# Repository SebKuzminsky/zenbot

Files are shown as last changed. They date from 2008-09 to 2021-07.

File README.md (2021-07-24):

This configuration is for the Zenbot CNC Mini Router (2007 version)
with 7i30 driver board, using the Mesa 5i23 for pwm generation &
quadrature counting.

Each axis/joint is run by a servo controlled by a 7i30.  All the servos
have no index channel, instead the index channel is used for home/limit
switches, plus the tool length offset switch.

# Spindle

The spindle is a TB-350S from Wolfgang Engineering (Richard?).

Rated for 0.0001 runout expected, 0.0004 runout max.

20,000 or 25,000 RPM, it's unclear.

Chris Radek has one, and has worked out how to replace the spindle
bearings.

The spindle uses an O-ring as a drive belt.  I got these from the local
hardware store, both seem to work:

* 2 1/16" OD, 1 7/8" ID, 3/32" wall
* 2 1/8" OD 1 7/8" ID, 1/8" wall

# Work holding

There is not much cutting force on the work, the main job of work holding
is to keep the copper surface parallel to XY across the whole work piece.

I used Target or Scotch branch "permanent double sided tape", it seemed
to work.

FIXME: note new tape, easier to work with since it has paper backing on
one side

Chris Radek says:

    I use the thicker tape with filaments in it that's meant for making
    very poor quality installations of tile or maybe carpet?

    Duck brand "Indoor Heavy Duty Carpet Tape"

    <https://www.findtape.com/shop/product-images.aspx?pid=646>

Try NYC CNC's technique of "blue painter's tape/ca/blue painter's tape":
<https://www.youtube.com/watch?time_continue=628&v=r6DCvtcU8_M>

# Z touch off

Bring the tool down close to the work, then raise it 0.001 at a time
until you can just barely roll a precision ground dowel pin between the
tool and the work.  The pins at SSD have a diameter of 0.250 +- 0.001.

If you don't have a dowel pin, the shank of a cutter works too but make
sure you measure the actual diameter carefully.

# Copper clad board

The work table can hold up to 4" x 6" boards.

I've been using MG Chemicals #506:

    Proto Board Copper Clad FR4
    Single Sided
    1 oz.
    6.00" x 4.00" (152.4mm x 101.6mm)
    the copper layer is 0.0014 inch (0.036 mm) thick
    the board is 1.6 mm (.0630 inch) thick

$7.14 from Digi-Key.

# Cutting Tools with Speeds and Feeds

## PreciseBits RCC08-0315-026F

Fish-tail chip breaker router bit, 0.0315 diameter, 0.256 depth of cut.

Speed: 24,000
Feed: 5 ipm, 125 mm/min
Plunge feed: 2.5 ipm, 62 mm/min

<https://www.precisebits.com/products/carbidebits/fcrouter.asp?product_id=713>
<https://www.precisebits.com/products/carbidebits/fdrouter.asp?product_id=742>

$4.77

## PreciseBits MN208-0100-002F

2-flute endmill, 0.010 diameter, 0.015 depth of cut.

Speed: 24,000
Feed: 2.4 ipm, 60 mm/min
Plunge feed: 1.2 ipm, 30 mm/min

<https://www.precisebits.com/products/carbidebits/precisebit-stub.asp?product_id=564>
<https://www.precisebits.com/products/carbidebits/precisebit-stub.asp?product_id=567>

$21

## Accupro 0.010" endmill (MSC #37290426)

0.010" diameter 2-flute carbide endmill, 0.015" LOC, 1/8" Shank
Uncoated, Spiral Flute, 30° Helix, Centercutting, Right Hand Cut, Right Hand Flute

MSC prices:
    List Price $23.99
    Your Price $14.87 ea.

## Accupro 0.010" endmill (long) (MSC #37289451)

0.010" diameter 2-flute carbide endmill, 0.030" LOC, 1/8" Shank
Uncoated, Spiral Flute, 30° Helix, Centercutting, Right Hand Cut, Right Hand Flute

MSC prices:
    List Price $23.99
    Your Price $14.87 ea.

## Reference info from Kyocera

### Old

<http://web.archive.org/web/20200128073523/http://www.kyoceraprecisiontools.com/micro/speeds-feeds/micro-end-mills-in.html>

Click on "Technical Info", then "Speeds & Feeds", then select "Standard
Carbide Micro End Mills (Inch)" with the appropriate diameter range.

### New

<https://www.kyocera-sgstool.com/digital-catalog>

Select a micro endmill and look at "Literature 1", cached in "datasheets":

## My conclusions

* Ap = Axial engagement
* Ae = Radial engagement

### Solid carbide endmills (d=0.010 inch) in soft copper alloy (Bronze, 300-350 sfm)

* ipt (roughing, Ap=1.0d, Ae=0.3d): 0.00004-0.00008
* ipt (finishing, Ap=1.0d, Ae=0.1d): 0.00008-0.00016
* ipt (slotting, Ap=0.5d, Ae=1.0d): 0.00003-0.00005

#### Slotting (5 thou deep, 10 thou wide)

feed rate (inch):

* `0.00003 inch/tooth * 2 tooth/rev * 24000 rev/min`
* `0.00006 inch/rev * 24000 rev/min`
* `1.44000 inch/min`

feed rate (metric):

* `1.44000 inch/min * 25.4 mm/inch`
* `36.6 mm/min`

SFM:

* cutter circumference = 0.031415 inch = 0.0026179939 feet
* spindle speed = 24,000 rev/min
* `0.00262 feet/rev * 24000 rev/min`
* `62.8318536 sfm`, way too low but what can you do

### Solid carbide endmills (d=0.010) in hard copper alloy (Brass 240-290 sfm)

Not recommended.

# Toolchain

KiCAD -> FlatCAM -> LinuxCNC

## KiCAD

### Schematic Capture

Design the circuit, save.

Export netlist in pcbnew format.

### PCB Layout

In the schematic editor, click the "Run Pcbnew" tool icon, or
Tools->Update PCB.

In "Setup -> Design Rules..." set "Clearance" and "Track Width" to
reasonable numbers for your machine and tooling.  "Clearance" is the
isolation between traces, should be at least slightly more than the
diameter of your cutting tool.  "Track Width" is trace width.

Use Mounting Hole footprints for mounting holes.

Draw the board outline as a "graphic polygon" on the Edge.Cuts layer.
When we generate gcode for this layer in FlatCAM later, the outside
of the polygon will be cut but the inside will not.  If you draw the
board edge as a collection of "graphic line" and "graphic arc" objects
both inside and outside will be cut, as if the outline were a trace.
It can be fixed in CAM by deleting the inside gcode, but using "graphic
polygon" is simpler.

Use "Place -> Drill and Place Offset" (or select the "place auxiliary
axis origin" tool) to set the origin of the project to the lower left
corner of the board.

To export to FlatCAM or other board fabrication tools:

    File -> Plot

        enable "Use auxiliary axis as origin"

        select the layers (B.Cu, Edge.Cuts), Plot (makes a `.gbr` gerber
        file for each layer).

        "Generate Drill Files...", enable "PTH and NPTH holes in single
        file", "Generate Drill File" (makes `.drl` file).

## FlatCAM (8.994 BETA)

### One-time Setup

At startup, before loading any project Gerber or Excelleon files, set
up some options.  Open the "Preferences" tab ("Edit" -> "Preferences").

#### "Preferences" -> "General" tab

* Set "Units" to "mm", to match what KiCad puts out.

#### "Preferences" -> "GERBER" tab, "Gerber General" section

* Set "Units" to "mm", to match what KiCad puts out.

#### "Preferences" -> "EXCELLON" tab, "Excellon General" section

* Set "Units" to "mm".

#### "Preferences" -> "EXCELLON" tab, "Excellon Options" section

* Set "Operation" to "Milling".

* Set "Milling Type" to "Both".

* Set "Milling Diameter" to 0.794 mm to match the diameter of the cutter
  we'll be milling holes with.

* Set "Drill Tool dia" to 0.794 mm to match the diameter of the cutter
  we'll be milling holes with.

* Set "Slot Tool dia" to 0.794 mm to match the diameter of the cutter
  we'll be milling holes with.

#### "Preferences" -> "GEOMETRY" tab, "Geometry Options" section

* FIXME: Set "Cut Z" to something?

* Set "Travel Z" to 0.5 mm, comfortably above the work.

* Set "Feedrate X-Y" to 36.6 mm/min (or whatever's appropriate for the
  cutter you're using).

* Set "Feedrate Z" to 15 mm/min (or whatever's appropriate for the cutter
  you're using).

* Set "Spindle speed" to 24000 rpm.

#### "Preferences" -> "CNC-JOB" tab, "CNC Job Adv. Options" section

* Set "Controller" to "LinuxCNC".

#### "Preferences" -> "CNC-JOB" tab, "CNC Job Editor" section

* Set "Prepend to G-Code" to "G21 G64 P0.01" for mm.

* Set "Append to G-Code" to "M2".

#### "Preferences" -> "TOOLS" tab, "Isolation Tool Options" section

* Set "Tools Dia" to 0.254 mm (0.010 inch) which matches the "PreciseBits
  MN208-0100-002F" endmill i'm using.

* FIXME: Set "Cut Z" to -0.127 mm (0.005 inch) which matches the
  axial depth-of-cut recommended for slotting with the "PreciseBits
  MN208-0100-002F" endmill i'm using.

* Set "Tools Type" to "Circular".

* Set "Passes" to 2.

* Set "Overlap" to 15% (this is in percent of the tool diameter).

* Check the "Combine" checkbox.

#### "Preferences" -> "TOOLS" tab, "Cutout Tool Options" section

* Set "Tool Diameter" to 0.800 mm (0.0315 inch) which matches the
  "PreciseBits RCC08-0315-026F" endmill i'm using for this cut.

* Set "Cut Z" to -1.8 mm, just enough to cut all the way through the
  circuit board.

* Uncheck "Multi-Depth".

* Set "Margin" to 0.000 mm (0.0 inch).

* Set "Gaps" to "None".  "Gaps" are work-holding tabs in the cutout
  tool path.  Since we're using double-sided tape for work holding no
  work-holding tabs are needed.

Click the `Apply` button at the bottom right, then the `Save` button at
the bottom right.

### Load PCB fabrication files

"Open Gerber" to load the 'back copper' and 'edge cuts' files.

"Open Excellon" to load the drill file.

### Mirror the bottom copper and the drill locations

In the "Project" tab, select the bottom copper object.

Switch to the "Properties" tab and click on the "Transformations" button.
This will create the "Transform Tool" tab and switch to it.

In the "Mirror (Flip)" section, click the "Flip on Y" button.

Repeat for the drill object.

### Generate trace isolation geometry from the back copper layer

From the "Tool" menu, select the "Isolation Tool".  This will create the
"Isolation Tool" tab and switch to it.

In the "GERBER" section, select the back copper object.

Click the "Generate Geometry" button.

In the resulting "Geometry Object", set these options:

* "Cut Z": Maybe -0.127 mm (-0.005 inch).  1 oz copper clad board has
  a 0.036 mm (0.0014 inch) thick copper layer, and it's pretty easy to
  mount the board with less than 0.076 mm (0.003 inch) wobble.  FIXME

* "Multi-Depth": disabled (since this cut is so shallow)

Note: "Travel Z", "Feedrate X-Y", "Feedrate Z" and "Spindle speed" should be set correctly
from the default settings we set up earlier.

Click "Generate CNCJob object".

In the resulting "CNC Job Object", click "Save CNC Code".

### Generate geometry for the board outline

From the "Tool" menu, select the "Cutout PCB" tool.  This will create the
"Cutout Tool" tab and switch to it.

In the "Source Object" section, select the edge cuts object.

Verify settings, they should all be correct from the defaults we set
up earlier.

Click the "Generate Geometry" button (either one seems to work).

Back in the "Project" tab, double-click on the edge cuts geometry object.

Verify parameters:

* "Cut Z" should be -1.800 mm, to cut all the way through the board.

* Enable "Multi-Depth" and set the depth to 0.650 mm.  FIXME

### Problems/bugs/issues

* G-code filename extension is .nc, should be .ngc

* Disable tool changes

* Rapid down to close to the work before switching to feed moves, it takes forever.

* helix milling doesn't work?

**OK to here**

**Notes** Standardize the cutting tools:

    isolation:
        carbide
        2-flute, sq
        dia: 0.010 inch, 0.254 mm
        loc: 1.5d, 0.015 inch, 0.356 mm
        Fz (fpt):
            DC 0.005: 0.000048 inch, 0.0012192 mm
            DC 0.010: 0.000099 inch, 0.0025146 mm
            DC 0.016: 0.000150 inch, 0.0038100 mm
        slotting Ap (axial depth of cut): up to 0.2 DC

        FIXME: consider 4-flute, ball?

    edge & holes:
        carbide
        4-flute, sq (FIXME?)
        dia: 0.0313 inch, 0.794 mm
        loc: 3d, 0.0938 inch, 2.382 mm
        Fz (fpt):
            DC 

        FIXME: what's the smallest diameter hole we'll need to helix-mill?
        whatever the finest lead we'll want to support is.  The smallest
        hole in the BP spindle encoder board is 0.800 mm

#### If you drew the board edge as a graphic polygon

Click "Board cutout" -> "Generate Geometry".

In the resulting "Geometry Object", set these options:

* "Cut Z": Maybe -1.800 mm (-0.070 inch).  1 oz copper clad board is
  about 0.065" thick, so this should cut through with a reasonable margin.

* "Feed Rate": 127 mm/min (5.0 inch/min)

* "Multi-Depth": enabled

* "Depth/pass": 0.5 mm (0.200 inch)

Note: "Travel Z", "Tool dia", and "Spindle speed" should all have correct
values from the application defaults we set earlier.

Click "Create CNC Job" -> "Generate".

In the resulting "CNC Job Object", click "Export G-Code".

#### If you drew the board edge as graphic lines & arcs

* `isolate breakout-board-Edge.Cuts.gbr -outname outline-iso`
* `exteriors outline-iso -outname outline`
* `delete outline-iso`
* `delete breakout-board-Edge.Cuts.gbr_iso`

### Mill holes

In the Project tab, select the drill object.

Switch to the "Selected" tab.

Find the "Mill Holes" section.

Verify that "Tool dia" has the correct default value of 0.800 mm (0.0315
inch) (to match the "PreciseBits RCC08-0315-026F" endmill i'm using for
this cut).

Click "Mill Holes" -> "Generate Geometry".

In the resulting "CNC Job Object", set these options:

* "Cut Z": Maybe -1.800 mm (-0.070 inch).  1 oz copper clad board is
  about 0.065" thick, so this should cut through with a reasonable margin.

* "Feed Rate": 100 mm/min (4.0 inch/min)

* "Tool dia": 0.800 mm (0.0315 inch)

* "Multi-Depth": enabled

* "Depth/pass": 0.5 mm (0.200 inch)

Note: "Travel Z" and "Spindle speed" should have the correct default
values from Application Options.

Click "Create CNC Job" -> "Generate".

In the resulting "CNC Job Object", click "Export G-Code".

## FlatCAM (old `master`)

At startup, before loading any project Gerber or Excelleon files, set
up some options.  Switch to the "Options" tab and select "APPLICATION
DEFAULTS".

Set "Units" to mm, to match what KiCad puts out.

In the "Gerber Options" section:

* In "Isolation Routing":

    * Set "Tool dia" to 0.254 mm (0.010 inch) which matches the
      "PreciseBits MN208-0100-002F" endmill i'm using.

    * Set "Width (# passes)" to 2.

    * Set "Pass overlap" to 0.15 (this is in percent of the tool
      diameter).

    * Check the "Combine Passes" checkbox.

* In "Board cutout":

    * Set "Tool dia" to 0.800 mm (0.0315 inch) which matches the
      "PreciseBits RCC08-0315-026F" endmill i'm using for this cut.

    * Set "Margin" to 0.000 mm (0.0 inch).

    * Set "Gap size" to 0.000 mm (0.0 inch), since we're using
      double-sided tape for work holding no work-holding tabs are needed.
      FlatCAM imposes a minimum size so we can't get totally rid of them.

    * Set "Gaps" to "2 (L/R)" or whatever feels appropriate to you.
      Since we don't want board cutout gaps and there's no "0" option
      here, you should probably choose one of the 2-gap options.

In the "Excelleon Options" section:

* In "Create CNC Job":

    * Set "Cut Z" to -1.8 mm, just enough to cut all the way through
      the circuit board.

    * Set "Travel Z" to 0.5 mm.

    * Set "Feed Rate" to 125 mm/min.

* In "Mill Holes" section:

    * Set "Tool dia" to 0.794 mm to match the diameter of the cutter
      we'll be milling holes with.

In the "Geometry Options" section:

* In "Create CNC Job":

    * Set "Travel Z" to 0.5 mm.

    * Set "Spindle Speed" to 24,000 rpm.

    Those two options are the same for every operation, so it's useful
    to set the defaults.  The other options will need to change depending
    on the operation, so the defaults are not useful.

In the "CNC Job Options" section:

* In "Export G-Code":

    * Set "Prepend to G-Code": "G21 G64 P0.01" for mm, or "G20 G64
      P0.0005" for inch.

    * Set "Append to G-Code": "m2"

    * Disable "Dwell".

Go to "File" -> "Save Defaults".  If you changed any of the application
settings you have to quit FlatCAM and restart for them to take effect.

### Load PCB fabrication files

"Open Gerber" to load the 'back copper' and 'edge cuts' files.

"Open Excellon" to load the drill file.

### Mirror the bottom copper and the drill locations

Select "Tool" -> "Double-Sided PCB Tool".

In "Bottom Layer", select the bottom copper gerber.

Set "Mirror Axis" to "Y".

Set "Axis Location" to "Box".

Set "Point/Box" to the edge cuts gerber.

Click "Mirror Object".

In "Bottom Layer", select the excelleon drill file.

Click "Mirror Object".

### Generate trace isolation geometry from the back copper layer

In the Project tab, select the B.Cu object.

Switch to the "Selected" tab.

Click "Isolation Routing" -> "Generate Geometry".

In the resulting "Geometry Object", set these options:

* "Cut Z": Maybe -0.051 mm (-0.002 inch).  1 oz copper clad board has
  a 0.036 mm (0.0014 inch) thick copper layer, and it's pretty easy to
  mount the board with less than 0.076 mm (0.003 inch) wobble.

* "Feed Rate": 60.1 mm/min (2.4 inch/min)

* "Multi-Depth": disabled (since this cut is so shallow)

Note: "Travel Z", "Tool dia" and "Spindle speed" should be set correctly
from the application defaults we set up earlier.

Click "Create CNC Job" -> "Generate".

In the resulting "CNC Job Object", click "Export G-Code".

### Generate geometry for the board outline

In the Project tab, select the Edge.Cuts object.

Switch to the "Selected" tab.

#### If you drew the board edge as a graphic polygon

Click "Board cutout" -> "Generate Geometry".

In the resulting "Geometry Object", set these options:

* "Cut Z": Maybe -1.800 mm (-0.070 inch).  1 oz copper clad board is
  about 0.065" thick, so this should cut through with a reasonable margin.

* "Feed Rate": 127 mm/min (5.0 inch/min)

* "Multi-Depth": enabled

* "Depth/pass": 0.5 mm (0.200 inch)

Note: "Travel Z", "Tool dia", and "Spindle speed" should all have correct
values from the application defaults we set earlier.

Click "Create CNC Job" -> "Generate".

In the resulting "CNC Job Object", click "Export G-Code".

#### If you drew the board edge as graphic lines & arcs

* `isolate breakout-board-Edge.Cuts.gbr -outname outline-iso`
* `exteriors outline-iso -outname outline`
* `delete outline-iso`
* `delete breakout-board-Edge.Cuts.gbr_iso`

### Mill holes

In the Project tab, select the drill object.

Switch to the "Selected" tab.

Find the "Mill Holes" section.

Verify that "Tool dia" has the correct default value of 0.800 mm (0.0315
inch) (to match the "PreciseBits RCC08-0315-026F" endmill i'm using for
this cut).

Click "Mill Holes" -> "Generate Geometry".

In the resulting "CNC Job Object", set these options:

* "Cut Z": Maybe -1.800 mm (-0.070 inch).  1 oz copper clad board is
  about 0.065" thick, so this should cut through with a reasonable margin.

* "Feed Rate": 100 mm/min (4.0 inch/min)

* "Tool dia": 0.800 mm (0.0315 inch)

* "Multi-Depth": enabled

* "Depth/pass": 0.5 mm (0.200 inch)

Note: "Travel Z" and "Spindle speed" should have the correct default
values from Application Options.

Click "Create CNC Job" -> "Generate".

In the resulting "CNC Job Object", click "Export G-Code".

# FlatCAM fixes

* Actual helix milling for the holes

* Ramp entry on multi-depth paths.

* Shouldn't `G0X0Y0` at the end.  (Fixed in 8.994?)

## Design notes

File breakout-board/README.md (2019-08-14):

This is a breakout board for connecting the Zenbot to a Mesa FPGA board.

It connects to a standard 50-pin ribbon cable from the Mesa FPGA board.

It passes the servo pins for channels 0, 1, and 2 to a second 50-pin
connector, for connecting to the 7i30 and driving the X, Y, and Z servos.

The remaining FPGA connector pins are routed to screw terminals, for
additional IO (eg the control line for an SSR to power the spindle).

The servo control pins are:

    1-23, 29, 31, 35, 39, 43, 47 (and 49)

The GPIO pins are:

    25, 27, 33, 37, 41, 45 (and 49)

The male 50-pin connectors are TE Part #1-5499923-0

The screw terminals are Phoenix Contact Part #1725711, "MPT 0,5/ 8-2,54"

# Fabrication

1. Mount a piece of single-sided 1 oz copper clad board to the mill.
   Make sure it's level.

2. Insert a PreciseBits MN208-0100-002F cutter, touch off Z

3. Open the `outline.ngc` gcode file and touch off X and Y at the lower
   left corner of the work.

4. Safety glasses, hearing protection, and spindle on.

5. Run the `back-copper.ngc` gcode file.

6. Switch to the PreciseBits RCC08-0315-026F cutter, touch off Z but
   not X and Y.

7. Safety glasses, hearing protection, and spindle on.

8. Run `drill-mill.ngc`.

9. Run `outline.ngc`.

# Prototypes

## Prototype 0: d7a043c1

* Cut deeper!  Some of the cuts didn't remove all the copper.

* The resistor lead holes should be a little larger diameter.  The pins
  on the other four components (LED, screw terminal, 50-pin connectors)
  all fit well.

* Would it be useful to to connect the ground pins on the 50-pin
  connectors to the ground plane?

* The 2x25 connectors extend past the end of the board some.

## Prototype 1: 2033f8a4

### Design changes from previous prototype

* Use a resistor with fatter leads.

* Cut 0.010 deep instead of 0.008.

* Resize the board to be more compact, and so the 2x25 connectors fit.
  I can fit two prototypes on a 4x6 board now.

### Fabrication

Broke two 0.010 endmills while cutting `back-copper.ngc`.  The first time
I switched in a fresh tool and restarted from just before where it broke,
but that was my last spare and now the project is stalled again.

I guess the 0.010 axial depth of cut is too much, maybe make the cut in
two passes of 0.005 or so instead?

## Prototype 2: a6cbd07e

### Design changes

* Increase PCB trace isolation from 0.010" to 0.011", so i can optionally
  use larger (by 0.001, but still), cheaper endmills.

* Decrease isolation milling depth of cut from 0.010" to 0.006", hopefully
  i'll break fewer tools.  If it doesn't isolate properly (like it
  probably won't) i can always touch off Z deeper and rerun the program.

### Fabrication

First pass ran to completion, didn't break the cutter (yay!), but didn't
fully isolate the traces (as expected).

Moved Z down 0.005, reran the program.

It finished!  There were a lot of burrs on the edges of the cuts, some
that caused shorts between the traces or between the traces and the
untouched copper pour.  I scrubbed it with a scotchbrite pad and that
fixed it, it's good!

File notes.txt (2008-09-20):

Spindle mounting plate:
Hole pattern 3.25 x 1 (dremel)
1/4-20 screws
distance from plate to motor: as small as possible
    presently: about 1.5"

2x2.5 to mount to Z axis

request plate hole pattern 2x2, holes for 1/4-20 screws, ?? oversize

motor shaft measured .1967, datasheet .1968 (=5.00mm?)
coupler .197 / ~.25, OD tapered about .593-.6
depth of ~.25 = .52 ( - .05 for boring bar)

motor 4218l family 4218l-01-11
2A/ph 75 oz-in  1.2ohm/ph  2.6mH/ph   inertia 0.37 oz-in^2
http://www.linengineering.com/site/products/4218.html

current set was 50% (1.44vref), increased to 70% (2.00vref) when machine
started to stall on 9/2/2008

X screw length approx. 10 3/4 inches
Z screw length less than 7 inches
Y screw length less than 15 inches

switches (L-R):
blue/green
grey/black
yellow/orange

accessible table, counting by mounting holes:
    left  0 ...  8   right   -- accessible 1...7
    front 0 ... 12   back    -- accessible 1...8

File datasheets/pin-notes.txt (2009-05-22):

hm2: 1=step, 3=dir
     13=step, 15=dir
    25=step, 27=dir
zenbot: step=2 dir=3
    step=4 dir=5
    step=6 dir=7

27-3 dir    dir
25-2 step   step
15-5 dir
13-4 step
3-7  dir
1-6  step

gpio.###  p5 pin #
48        1
49        3
50        5
51	7
52	9
53	11
54	13
55	15
56	17
57	19
58	21
59	23
60	25
61	27
62	29
63	31
64	33        enables (rev2)
65	35        enables (rev2)
66	37        enables (rev2)
67	39        probe-in
68	41        x lim
69	43        y lim
70	45        z lim
71	47        spindle

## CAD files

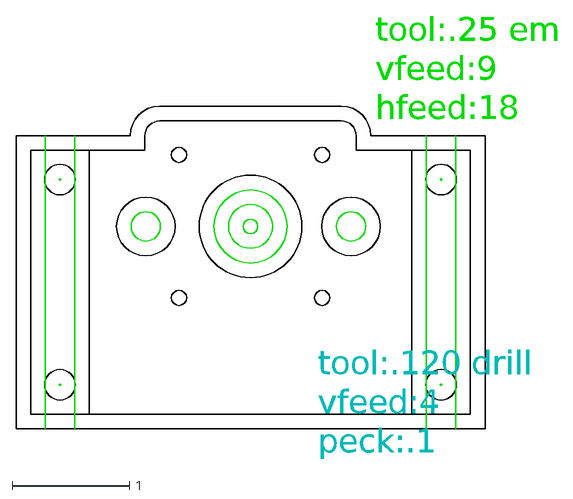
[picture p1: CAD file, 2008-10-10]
parts/zenbot.dxf
tool:.120 drill
vfeed:4
peck:.1
tool:.25 em
vfeed:9
hfeed:18

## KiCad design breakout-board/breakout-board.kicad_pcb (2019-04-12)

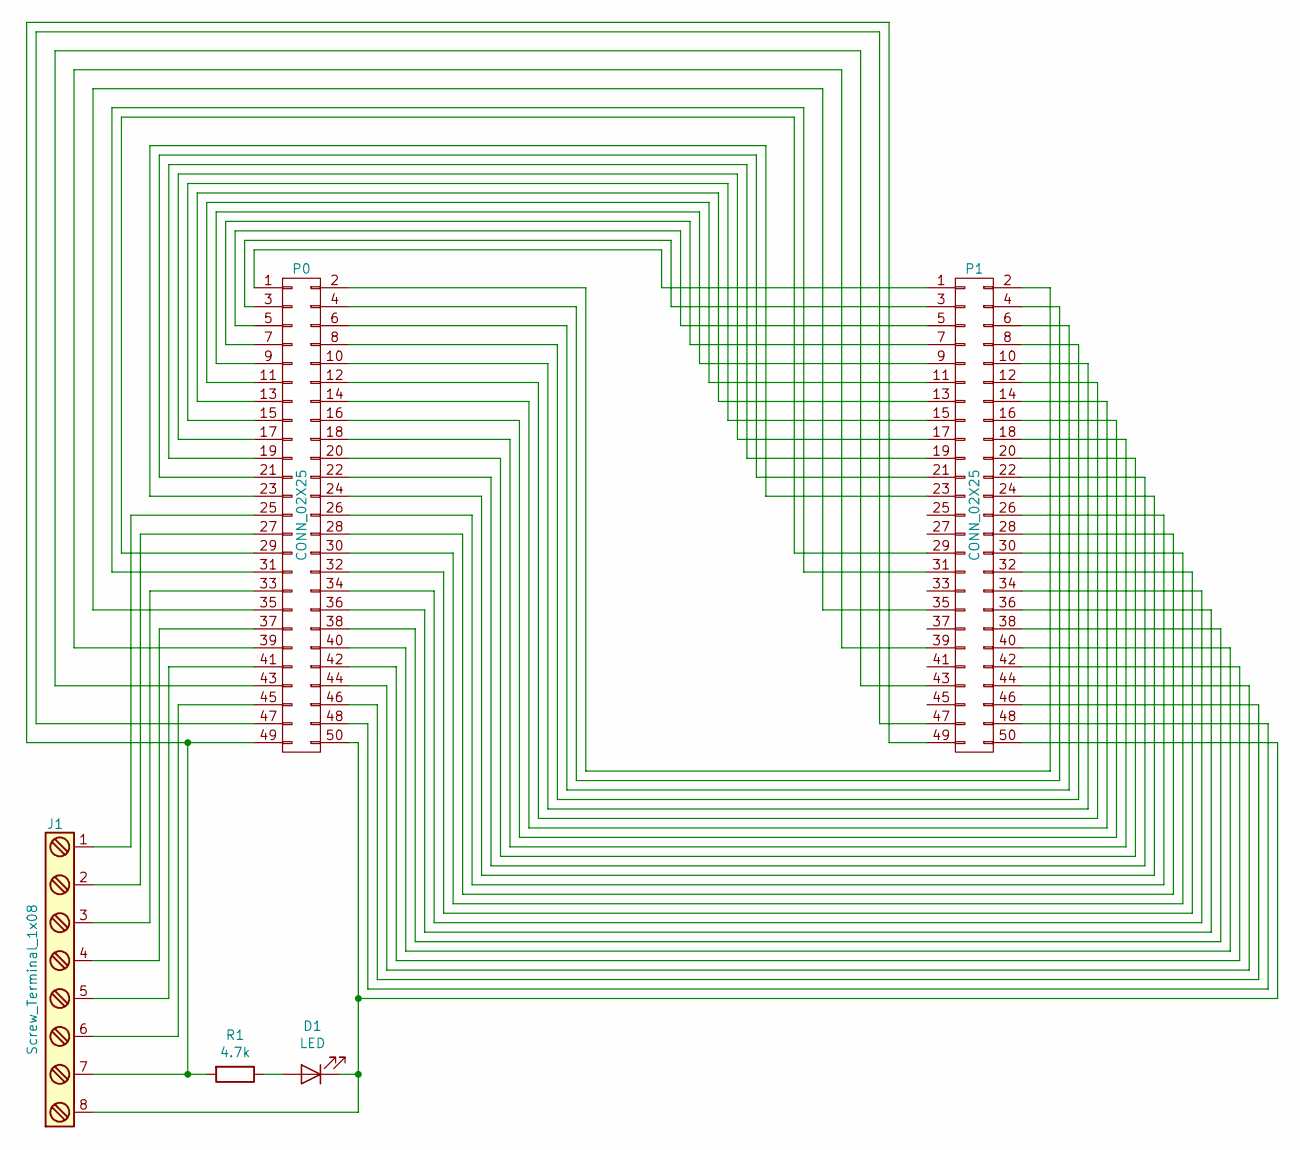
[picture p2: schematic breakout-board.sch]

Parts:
D1: LED; LED_D5.0mm
J1: Screw_Terminal_1x08; TerminalBlock_Phoenix_MPT-0,5-8-2.54_1x08_P2.54mm_Horizontal
P0, P1: CONN_02X25; TE-Connectivity_1-5499923-0
R1: 4.7k; R_Axial_DIN0411_L9.9mm_D3.6mm_P15.24mm_Horizontal

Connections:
unnamed: D1.1 (K), J1.8, P0.50, P1.50
unnamed: D1.2 (A), R1.1
unnamed: J1.1, P0.25
unnamed: J1.2, P0.27
unnamed: J1.3, P0.33
unnamed: J1.4, P0.37
unnamed: J1.5, P0.41
unnamed: J1.6, P0.45
unnamed: J1.7, P0.49, P1.49, R1.2
unnamed: P0.1, P1.1
unnamed: P0.2, P1.2
unnamed: P0.3, P1.3
unnamed: P0.4, P1.4
unnamed: P0.5, P1.5
unnamed: P0.6, P1.6
unnamed: P0.7, P1.7
unnamed: P0.8, P1.8
unnamed: P0.9, P1.9
unnamed: P0.10, P1.10
unnamed: P0.11, P1.11
unnamed: P0.12, P1.12
unnamed: P0.13, P1.13
unnamed: P0.14, P1.14
unnamed: P0.15, P1.15
unnamed: P0.16, P1.16
unnamed: P0.17, P1.17
unnamed: P0.18, P1.18
unnamed: P0.19, P1.19
unnamed: P0.20, P1.20
unnamed: P0.21, P1.21
unnamed: P0.22, P1.22
unnamed: P0.23, P1.23
unnamed: P0.24, P1.24
unnamed: P0.26, P1.26
unnamed: P0.28, P1.28
unnamed: P0.29, P1.29
unnamed: P0.30, P1.30
unnamed: P0.31, P1.31
unnamed: P0.32, P1.32
unnamed: P0.34, P1.34
unnamed: P0.35, P1.35
unnamed: P0.36, P1.36
unnamed: P0.38, P1.38
unnamed: P0.39, P1.39
unnamed: P0.40, P1.40
unnamed: P0.42, P1.42
unnamed: P0.43, P1.43
unnamed: P0.44, P1.44
unnamed: P0.46, P1.46
unnamed: P0.47, P1.47
unnamed: P0.48, P1.48

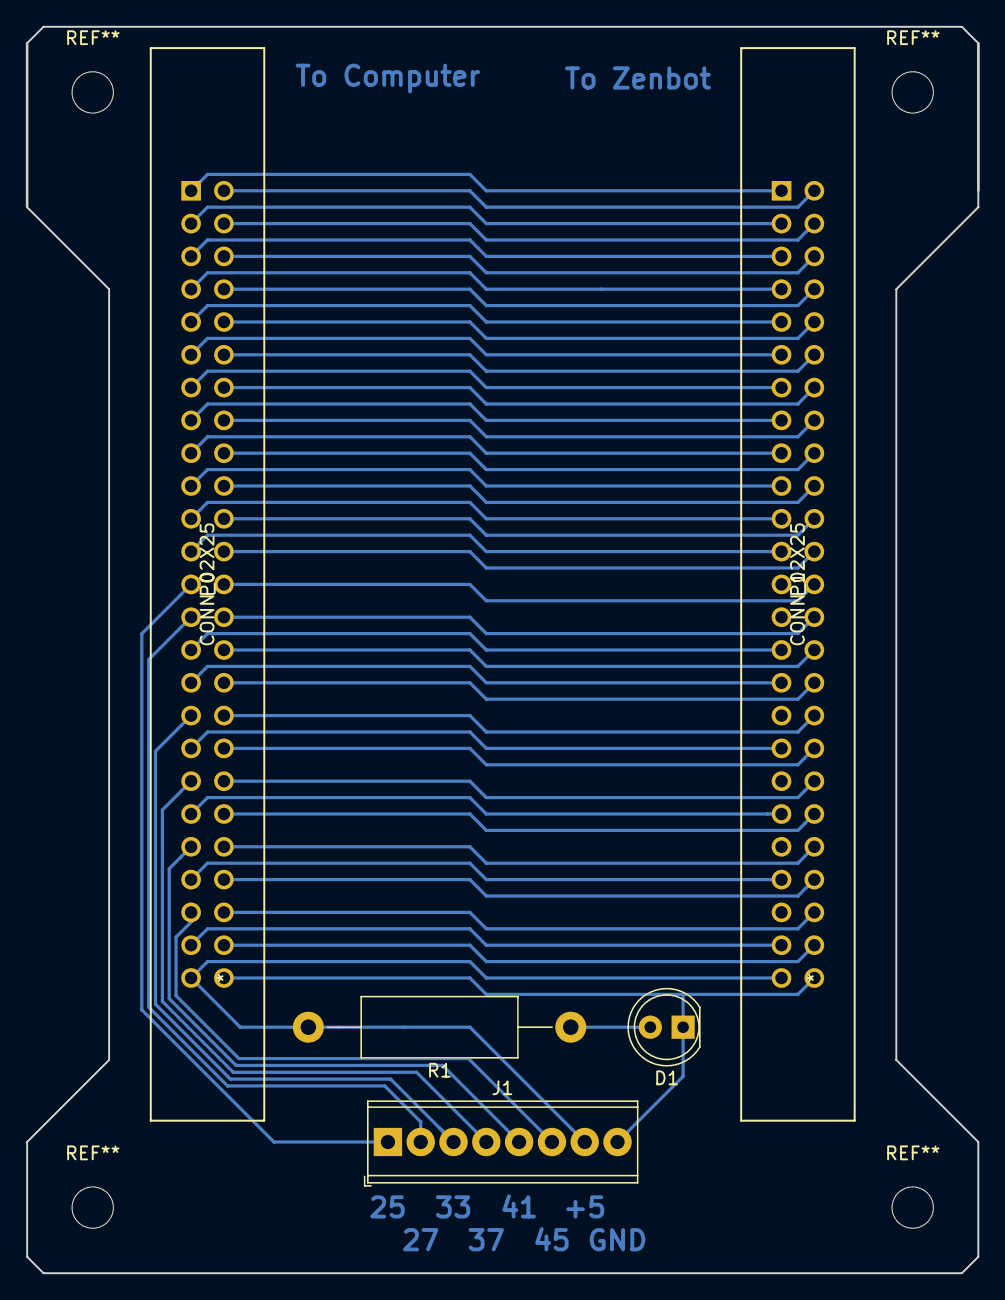
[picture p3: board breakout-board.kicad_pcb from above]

Board: 2 copper layers, 73.7 x 96.5 mm, 5 parts (0 on the bottom side), 51 nets.

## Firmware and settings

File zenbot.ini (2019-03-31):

[EMC]
MACHINE =                     zenbot
NML_FILE =                    emc.nml
DEBUG =                       0x7fffffff

[DISPLAY]
DISPLAY =                     axis
POSITION_OFFSET =             RELATIVE
POSITION_FEEDBACK =           ACTUAL
MAX_FEED_OVERRIDE =           2.0
PROGRAM_PREFIX =              /home/seb/zenbot
INTRO_GRAPHIC =               logo.gif
INTRO_TIME =                  5
EDITOR =                      gvim
INCREMENTS =                  1.000, 0.100, 0.010, 0.001, 0.0001

DEFAULT_LINEAR_VELOCITY =     .25

[FILTER]
PROGRAM_EXTENSION =           .png,.gif,.jpg Grayscale Depth Image
PROGRAM_EXTENSION =           .py Python Script

png =                         image-to-gcode
gif =                         image-to-gcode
jpg =                         image-to-gcode
py =                          python

[TASK]
TASK =                        milltask
CYCLE_TIME =                  0.010

[RS274NGC]
PARAMETER_FILE =              stepper.var

[EMCMOT]
EMCMOT =                      motmod
SHMEM_KEY =                   111
COMM_TIMEOUT =                1.0
COMM_WAIT =                   0.010
PERIOD =                      1000000

[HAL]
HALFILE =                     5i23.hal
POSTGUI_HALFILE =             postgui.hal

[TRAJ]
AXES =                        3
COORDINATES =                 X Y Z
HOME =                        0 0 0
LINEAR_UNITS =                inch
ANGULAR_UNITS =               degree
CYCLE_TIME =                  0.010
DEFAULT_VELOCITY =            0.6
MAX_VELOCITY =                0.65
POSITION_FILE =               position.txt

[AXIS_0]
TYPE =                        LINEAR
HOME =                        0
MAX_VELOCITY =                0.5
MAX_ACCELERATION =            5.0
BACKLASH =                    0.000
INPUT_SCALE =                 -74666.67
OUTPUT_SCALE =                -1.000
MIN_LIMIT =                   -.05
MAX_LIMIT =                   6.20
FERROR =                      0.010
MIN_FERROR =                  0.005
HOME_OFFSET =                 -.05
HOME_SEARCH_VEL =             -.2
HOME_LATCH_VEL =              -.1
HOME_FINAL_VEL =              0.5
HOME_USE_INDEX =              NO
HOME_IGNORE_LIMITS =          NO
HOME_SEQUENCE =               1
HOME_IS_SHARED =              1
P = 225
I = 20
D = 2
FF1 = 0.4
FF2 = 0.0
DEADBAND = 5e-06
IDEADBAND = 0.005

[AXIS_1]
TYPE =                        LINEAR
HOME =                        0
MAX_VELOCITY =                0.5
MAX_ACCELERATION =            5.0
BACKLASH =                    0.000
INPUT_SCALE =                 -74666.67
OUTPUT_SCALE =                1.000
MIN_LIMIT =                   -.01
MAX_LIMIT =                   6.80
FERROR =                      .005
MIN_FERROR =                  .001
HOME_OFFSET =                 -.02
HOME_SEARCH_VEL =             -.3
HOME_LATCH_VEL =              -.1
HOME_FINAL_VEL =              0.3
HOME_USE_INDEX =              NO
HOME_IGNORE_LIMITS =          NO
HOME_SEQUENCE =               2
HOME_IS_SHARED =              1
P = 250
I = 20
D = 2
FF1 = 0.22
FF2 = 0.003
DEADBAND = 5e-06
IDEADBAND = 0.005

[AXIS_2]
TYPE =                        LINEAR
HOME =                        0.0
MAX_VELOCITY =                0.20
MAX_ACCELERATION =            1.5
BACKLASH =                    0.000
INPUT_SCALE =                 74666.67
OUTPUT_SCALE =                -1.000

# good:
#MIN_LIMIT =                   -3.275
# bad:
#MIN_LIMIT =                   -3.3
MIN_LIMIT =                   -3.275
MAX_LIMIT =                   0.01
FERROR =                      0.050
MIN_FERROR =                  0.010
HOME =                        0 
HOME_OFFSET =                 0.02

# good:
#HOME_SEARCH_VEL =             .125
#HOME_LATCH_VEL =              .05
#HOME_FINAL_VEL =              0.5
# bad:
#HOME_SEARCH_VEL =             .15
#HOME_LATCH_VEL =              .1
#HOME_FINAL_VEL =              0.5
HOME_SEARCH_VEL =             .125
HOME_LATCH_VEL =              .05
HOME_FINAL_VEL =              0.5

HOME_USE_INDEX =              NO
HOME_IGNORE_LIMITS =          NO
HOME_SEQUENCE =               0
P = 250
I = 20
D = 2
FF1 = 0.22
FF2 = 0.003
DEADBAND = 5e-06
IDEADBAND = 0.005

[EMCIO]
EMCIO =                       io
CYCLE_TIME =                  0.100
TOOL_TABLE =                  stepper.tbl
TOOL_CHANGE_POSITION =        3 0 0

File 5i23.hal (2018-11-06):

loadrt trivkins
loadrt [EMCMOT]EMCMOT base_period_nsec=[EMCMOT]PERIOD servo_period_nsec=[EMCMOT]PERIOD traj_period_nsec=[EMCMOT]PERIOD key=[EMCMOT]SHMEM_KEY num_joints=[TRAJ]AXES

loadrt hostmot2
loadrt hm2_pci config="firmware=hm2/5i23/SVST8_4.BIT num_encoders=3 num_pwmgens=3 num_stepgens=0"

show pin hm2_5i23

setp hm2_5i23.0.pwmgen.pwm_frequency 30000

loadrt pid num_chan=3
loadrt idb count=3
loadrt debounce cfg=2
loadrt ddt count=6

show pin hm2_5i23.0.encoder.01
net Xpos-cmd axis.0.motor-pos-cmd => pid.0.command
net Xpid-cmd pid.0.output => idb.0.in
net Xpwm-cmd idb.0.out => hm2_5i23.0.pwmgen.00.value
net Xpwm-ena axis.0.amp-enable-out => hm2_5i23.0.pwmgen.00.enable pid.0.enable

net Ypos-cmd axis.1.motor-pos-cmd => pid.1.command
net Ypid-cmd pid.1.output => idb.1.in
net Ypwm-cmd idb.1.out => hm2_5i23.0.pwmgen.01.value
net Ypwm-ena axis.1.amp-enable-out => hm2_5i23.0.pwmgen.01.enable pid.1.enable

net Zpos-cmd axis.2.motor-pos-cmd => pid.2.command
net Zpid-cmd pid.2.output => idb.2.in
net Zpwm-cmd idb.2.out => hm2_5i23.0.pwmgen.02.value
net Zpwm-ena axis.2.amp-enable-out => hm2_5i23.0.pwmgen.02.enable pid.2.enable


net Xpos-fb hm2_5i23.0.encoder.00.position => axis.0.motor-pos-fb pid.0.feedback
net Ypos-fb hm2_5i23.0.encoder.01.position => axis.1.motor-pos-fb pid.1.feedback
net Zpos-fb hm2_5i23.0.encoder.02.position => axis.2.motor-pos-fb pid.2.feedback

setp pid.0.Pgain [AXIS_0]P
setp pid.0.Igain [AXIS_0]I
setp pid.0.Dgain [AXIS_0]D
setp pid.0.FF1 [AXIS_0]FF1
setp pid.0.FF2 [AXIS_0]FF2
setp pid.0.deadband [AXIS_0]DEADBAND
setp idb.0.amount [AXIS_0]IDEADBAND

setp pid.1.Pgain [AXIS_1]P
setp pid.1.Igain [AXIS_1]I
setp pid.1.Dgain [AXIS_1]D
setp pid.1.FF1 [AXIS_1]FF1
setp pid.1.FF2 [AXIS_1]FF2
setp pid.1.deadband [AXIS_1]DEADBAND
setp idb.1.amount [AXIS_1]IDEADBAND

setp pid.2.Pgain [AXIS_2]P
setp pid.2.Igain [AXIS_2]I
setp pid.2.Dgain [AXIS_2]D
setp pid.2.FF1 [AXIS_2]FF1
setp pid.2.FF2 [AXIS_2]FF2
setp pid.2.deadband [AXIS_2]DEADBAND
setp idb.2.amount [AXIS_2]IDEADBAND

setp hm2_5i23.0.pwmgen.00.scale [AXIS_0]OUTPUT_SCALE
setp hm2_5i23.0.pwmgen.01.scale [AXIS_1]OUTPUT_SCALE
setp hm2_5i23.0.pwmgen.02.scale [AXIS_2]OUTPUT_SCALE

setp hm2_5i23.0.encoder.00.scale [AXIS_0]INPUT_SCALE
setp hm2_5i23.0.encoder.01.scale [AXIS_1]INPUT_SCALE
setp hm2_5i23.0.encoder.02.scale [AXIS_2]INPUT_SCALE

addf hm2_5i23.0.read servo-thread
addf debounce.0 servo-thread
addf motion-command-handler servo-thread
addf motion-controller servo-thread
addf pid.0.do-pid-calcs servo-thread
addf pid.1.do-pid-calcs servo-thread
addf pid.2.do-pid-calcs servo-thread
addf idb.0 servo-thread
addf idb.1 servo-thread
addf idb.2 servo-thread
addf hm2_5i23.0.write servo-thread

addf ddt.0 servo-thread
addf ddt.1 servo-thread
addf ddt.2 servo-thread
addf ddt.3 servo-thread
addf ddt.4 servo-thread
addf ddt.5 servo-thread

net tool-prep-loop iocontrol.0.tool-prepare => iocontrol.0.tool-prepared
net estop-loop iocontrol.0.user-enable-out iocontrol.0.emc-enable-in

#net spindle motion.spindle-on => hm2_5i20.0.gpio.071.out
#setp hm2_5i20.0.gpio.071.is_output 1

# tool length switch is on gpio 004

# xy shared home
show pin  hm2_5i23.0.gpio.005*
net xyhome-raw <= hm2_5i23.0.gpio.005.in_not => debounce.0.0.in
net xyhome-filtered debounce.0.0.out => axis.0.home-sw-in axis.1.home-sw-in

net zhome-raw <= hm2_5i23.0.gpio.017.in_not => debounce.0.1.in
net zhome-filtered debounce.0.1.out => axis.2.home-sw-in

loadusr -W hal_manualtoolchange

net tool-change hal_manualtoolchange.change iocontrol.0.tool-change 
net tool-changed hal_manualtoolchange.changed iocontrol.0.tool-changed
net tool-prep-number hal_manualtoolchange.number iocontrol.0.tool-prep-number

net Xpos-cmd => ddt.0.in
net Xvel ddt.0.out => ddt.1.in
net Xacc <= ddt.1.out

net Ypos-cmd => ddt.2.in
net Yvel ddt.2.out => ddt.3.in
net Yacc <= ddt.3.out

net Zpos-cmd => ddt.4.in
net Zvel ddt.4.out => ddt.5.in
net Zacc <= ddt.5.out

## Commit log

2007-12-06 for some time now, the doublestep mode has been activated by just setting stepspace to 0
    setting stepgen accel limits may improve behavior a bit
    [xylotex_pinout.hal]
2008-05-17 configuration to use pluto-step
    [pluto.hal]
2008-05-17 enables are nice
    [xylotex_pinout.hal]
2008-06-02 switch over to pluto -- whee, it works
2008-07-02 * correct for measured backlash * remove jogwheel setup, that board seems to have died
2008-07-05 It's total overkill, but now I'm using a servo motor with encoder attached to an m5i20 as the jog wheel.
    [jogwheel-post.hal, jogwheel-pre.hal, postgui.hal]
2008-07-16 for Y limit switch installed at rear of table
    [jogwheel-pre.hal, pluto.hal]
2008-07-17 homing for Y switch near front of table
    [pluto.hal]
2008-07-20 tool length sensor
    [pluto.hal]
2008-08-02 don't track these files
    [.scope.cfg]
2008-08-02 hackishly use mesa index inputs for homing
    [pluto.hal]
2008-08-07 restore backlash. add X, Y home switches
    [pluto.hal]
2008-08-13 fix jog slider limits. machine has started stalling at 1.2ipm, wtf
2008-08-14 switches now independent
    [pluto.hal]
2008-08-14 no need for 3 different periods. oh and no discernable benefit from 2kHz servo rate either
    [pluto.hal]
2008-08-14 I don't envision going back to software step generation
    [core_stepper.hal, xylotex_pinout.hal]
2008-08-16 g30 for tool length sensor with new spindle
2008-08-16 extended Z travel with new sensor
2008-09-01 spindle control and manual toolchange
    [pluto.hal]
2008-09-01 re-measure backlash. tool change position. stepper mpg
    [zenbot.ini]
2008-09-04 it's nice to have velocity and accel to scope
    [pluto.hal]
2008-09-04 changed spindle mounting which moved the TLS again
2008-09-07 tweak homing velocity. commented velocities were stable in testing
    .. but after a few thousand inches of tests, I noticed a bunch of metal
    shavings made from the same material as the nuts (brass?) so maybe going
    this fast is what they call a bad idea. I can't wait to get these screws
    and nuts replaced!
    [zenbot.ini]
2008-09-15 switching to ribbon cable for switch terminal board caused pin numbers to change
    [pluto.hal]
2008-09-18 new screws and nuts
2008-09-20 describe accessible area of table in terms of the mounting holes in the table
2008-10-08 datasheet for pancake servos
2008-10-10 switch datasheet
2008-10-10 some drawings and boss gcode files used to mill a replacement part for the zenbot
    [zenbot.dxf]
2008-10-11 Z home switch
    [pluto.hal]
2009-01-15 disable home switch until wiring can be made permanent
2009-01-29 make it work again after some system changes
    * m5i20 removed
    * rewired
    * added Z switch again
    [pluto.hal, postgui.hal]
2009-05-22 rev1 board to adapt to xylotex
    [5i20-xylotex-c.brd, 5i20-xylotex-c.sch]
2009-05-22 convert to 5i20
    [5i20.hal]
2009-05-22 rev1 board as milled
2009-05-22 swap axes around according to my temporary wiring
    [5i20.hal]
2009-05-22 temporarily disable home switches
2009-05-23 set pins to open drain to avoid ringing on rising edges
    [5i20.hal]
2009-05-23 continue hooking stuff back up
    [5i20.hal]
2009-05-23 saw a stall on X, lower all the limits a bit
    [zenbot.ini]
2009-07-05 boss gcode for motor mount
2009-07-07 make spindle work
    [5i20.hal]
2009-07-07 stepper stuff
    [5i20-xylotex-d.brd, 5i20-xylotex-d.sch, 5i20.hal]
2009-07-07 continued tuning
    [5i20.hal]
2009-07-11 a useful script to run one motor around
    [5i20-servo-test.hal]
2009-07-21 3-axis motion
    [5i20.hal]
2009-08-20 moved to first connector
2009-08-20 make homing work again
    [5i20.hal]
2010-05-28 useful for testing, not strictly related to zenbot
    [5i20-test.hal, 7i43-test.hal]
2010-05-28 some kind of exercise script?
    [runmotor.hal, runmotor2.hal]
2010-05-28 some kind of test script
    [test.hal]
2010-05-28 use a firmware with probe latch
    [5i20-servo-test.hal, 5i20.hal]
2010-05-28 firmware with probe latch
2018-11-03 remove redundant pin settings
    [5i20.hal]
2018-11-03 switch zenbot.ini to new 5i23 hal config, make it load on 2.7
    [5i23.hal]
2018-11-05 get rid of [AXIS_*](INSTANCE)
    [5i23.hal]
2018-11-06 move xy home switch to input 005
    [5i23.hal]
2018-11-06 slow everything down so it stops f-erroring
    This lets us home the machine so we can start tuning the servos.
    [zenbot.ini]
2018-11-07 ini: fix Y and Z limits
    [zenbot.ini]
2018-11-07 ini: tweak X pid tuning
2018-11-07 todo: more work on the spindle
2018-11-07 readme: add info on spindle
2018-11-21 start adding a breakout board
    [breakout-board.kicad_pcb, breakout-board.sch]
2018-11-22 more work on the breakout board
    [breakout-board.kicad_pcb, breakout-board.sch]
2018-11-25 save breakout-board from kicad 4.0
    [breakout-board.kicad_pcb, breakout-board.sch]
2018-11-25 update breakout board for kicad 5.0, add gerber & drill files
    [breakout-board.kicad_pcb, breakout-board.sch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]
2018-11-26 add proper mounting holes
    [breakout-board.kicad_pcb, breakout-board.sch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]
2018-11-28 compactify, add edge cuts, merge all drilled holes (plated and non-plated)
    [breakout-board.kicad_pcb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]
2018-11-28 README: add depth-of-cut info to tools
2018-12-03 ini: decrease Z max accel for reliability
    I should really tune the Y and Z PID loops
2018-12-03 ini: tune Z home velocities
2019-03-30 zenbot: make Z a little slower, avoid following errors
    [zenbot.ini]
2019-03-31 add datasheet for spindle SSR
2019-03-31 breakout-board: add notes on fabrication, & need to cut deeper
2019-04-06 breakout-board: added notes on the prototype i made
2019-04-08 add footprint for 2x25 connector
2019-04-08 README: better notes on KiCAD
2019-04-08 breakout-board: next prototype is ready
    [breakout-board.kicad_pcb, breakout-board.sch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]
2019-04-12 breakout-board: fix a copy/paste error
2019-04-12 breakout-board: failed to cut the board, again
2019-04-12 breakout-board: rework for lerger cutter, shallower DOC
    [breakout-board.kicad_pcb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]
2019-05-07 README: add info on MSC endmills & MG Chemicals copper-clad board
2019-05-08 breakout board README: note which commits the prototypes were made from
2019-05-08 breakout-board: prototype 2 back-copper looks good!
2019-07-30 README: add more info on pcb layout and flatcam
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2019-08-14 breakout-board README: fix a bug in XY touchoff
2020-01-29 add notes on the O-rings used as spindle drive belts
2021-07-17 README: add more info on the copper-clad board
2021-07-18 README: move copper clad board info up
